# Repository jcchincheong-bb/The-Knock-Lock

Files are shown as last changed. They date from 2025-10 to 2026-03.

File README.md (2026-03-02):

# Knock Lock

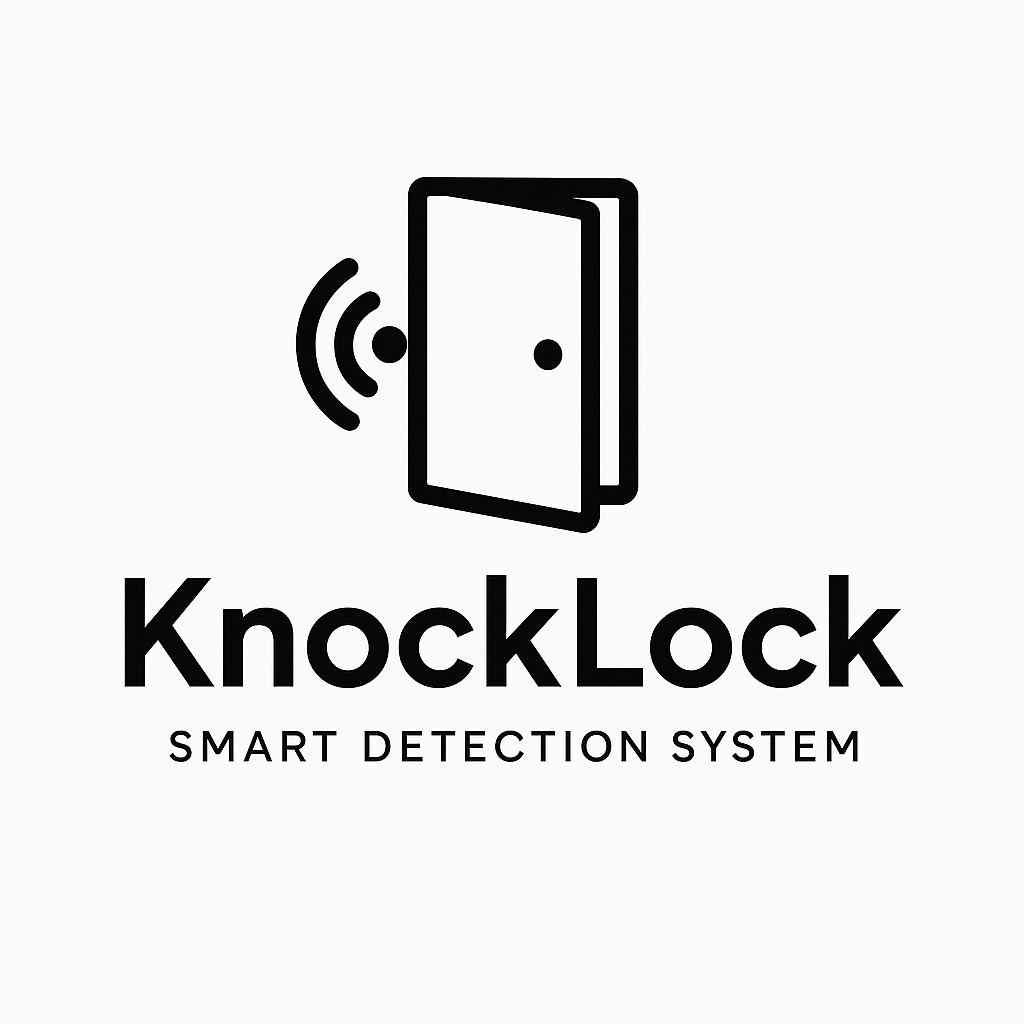
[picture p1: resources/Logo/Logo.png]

<!-- <div id="logo" align="center">
<figure>
  <img src="/resources/Logo/Logo.png" alt="Logo" width="400">
</figure>
</div> -->

As children, many of us might have invented secret knocks that we used to identify ourselves to our friends or siblings. But, what if those special codes could actually unlock the door itself? As adults, how many times have you forgotten your keys and wished you could just knock in a certain way and the door would unlock for you? As such, the aim of The Knock Lock project is to design and assemble a system that unlocks a door by recognising a specific knocking pattern. As a proof of concept, the system will be designed as a small lock box with the hope of extending the idea to work on a full door in the future.

This project was done as part of the course 2314 Practical Electronics at HSRW. The full project report can be found [here](https://github.com/AbhinavK02/Knock-Lock/blob/main/ProjectReport.md).

Knock Lock Product Showcase (https://www.youtube.com/watch?v=qGrgIr3oHPE)

<div align="center">
  <table border="0" style="width: 100%; border: none;">
    <tr>
      <td align="left" style="vertical-align: middle; width: auto; padding: 10px 0;">
        by: <a href="https://abhinavk02.github.io/">Abhinav Kothari</a> and <a href="https://jcchincheong-bb.github.io/">Justin Chin Cheong</a>
      </td>
      <td align="right" style="vertical-align: middle; width: 1%; white-space: nowrap; padding-left: 20px;">
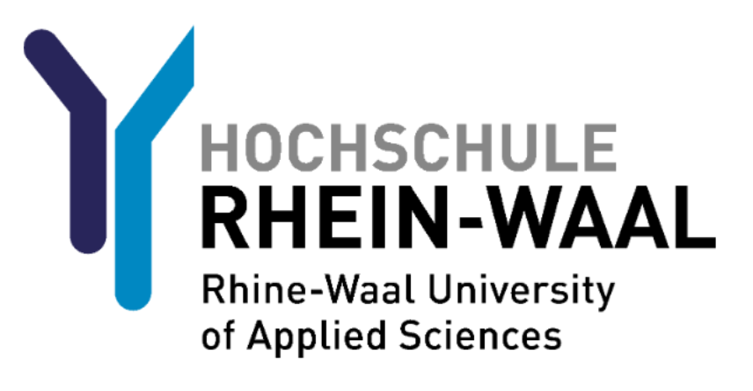
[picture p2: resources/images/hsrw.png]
HSRW Logo
        
      </td>
    </tr>
  </table>
  </figure>

</div>

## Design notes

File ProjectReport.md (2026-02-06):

<!----------------------------------------------------------------
<div id="logo" align="center">
<figure>
  <img src="/resources/images/Logo.png" alt="Logo" width="400">
  <figcaption align="center"><b>Figure 1:</b> Knock Lock Logo</figcaption>
</figure>
</div>

<div id="pcb-blank"  align="center">
  <figure>
  <table border="0">
    <tr>
      <td><figure>
        <img src="/resources/images/Unsoldered PCB.jpeg" height="200">
        <figcaption align="center"><b>(a):</b> Front </figcaption>
      </figure></td>
      <td><figure>
        <img src="/resources/images/Unsoldered PCB 2.jpeg" height="200">
        <figcaption align="center"><b>(b):</b> Back </figcaption>
      </figure></td>
    </tr>
  </table>
  <figcaption align="center"><b>Figure 5.8:</b> Final PCB without Components</figcaption>
  </figure>
</div>
----------------------------------------------------->
<!--
STOP CHANGING THE STRUCTURE! IT'S GOOD NOW!!!
-->
# Knock Lock

<div id="logo" align="center">
<figure>
  
</figure>
</div>

<div align="center">
  <table border="0" style="width: 100%; border: none;">
    <tr>
      <td align="left" style="vertical-align: middle; width: auto; padding: 10px 0;">
        by: <a href="https://www.linkedin.com/in/abhinav-kothari-2ak/">Abhinav Kothari</a> (33349) and <a href="https://jcchincheong-bb.github.io/">Justin Chin Cheong</a> (34140)
        <br><br>
        <strong>Faculty of Technology and Bionics</strong>
        <br><br>
        <em><strong>Rhine-Waal University of Applied Sciences</strong></em>
        <br><br>
        Date: 18 January 2026
      </td>
      <td align="right" style="vertical-align: middle; width: 1%; white-space: nowrap; padding-left: 20px;">
        HSRW Logo
      </td>
    </tr>
  </table>
  </figure>
</div>

<!-- by: [Abhinav Kothari](https://www.linkedin.com/in/abhinav-kothari-2ak/) (33349) and [Justin Chin Cheong](https://jcchincheong-bb.github.io/) (34140) -->

<!-- **Faculty of Technology and Bionics** -->

<!-- ***Rhine-Waal University of Applied Sciences*** -->

<!-- Date: 18 January 2022  -->

----

## Abstract

The Knock Lock project presents the design, implementation, and evaluation of a novel access control system that unlocks a small lock box through the recognition a user-defined knocking pattern. Motivated by the limitations of conventional key-based and electronic locking mechanisms, the system aims to provide a fun and intuitive alternative that does not rely on physical tokens or wireless credentials. Unlike most existing knock-based systems that use piezoelectric sensors, this project explores the use of a MEMS accelerometer for knock detection, enabling improved reliability, flexibility and multi-axis measurement.

Following a V-model design methodology, the system was developed from defined requirements through hardware, software, and housing design, to full system integration and testing. The final prototype consists of an ESP32-based controller, an accelerometer sensor, a servo-driven locking mechanism, a custom PCB, a user interface employing LEDs and a buzzer and a custom 3D printed housing. Verification and validation tests demonstrate reliable knock pattern recognition, successful locking and unlocking behaviour, effective power management with sleep modes, and positive user acceptance.

The results confirm the feasibility of accelerometer-based knock recognition for access control applications and highlight the potential for further development toward full-scale door locking systems and enhanced security features.

## Table of Contents

[[_TOC_]]
<!--------------------------------------------------------------------------------------------------------------------->
<!--------------------------------------------------------------------------------------------------------------------->
## 1 Introduction 
### 1.1 Rationale
As children, many of us might have invented secret knocks that we used to identify ourselves to our friends or siblings. But, what if those special codes could actually unlock the door itself? As adults, how many times have we forgotten your keys and wished you could just knock in a certain way to unlock the door? 

There are many different types of security systems on the market that use systems ranging from combinations to NFC, but there are no commercial products of this kind that unlock by recognising a specific knocking pattern. As such, the aim of The Knock Lock project is to design and assemble a system that unlocks a door by recognising a specific knocking pattern. As a proof of concept, the system is designed as a small lock box as shown in [Figure 1.1](#preliminary-sketch) with the hope of extending the idea to work on a full door in the future.

<div id="preliminary-sketch" align="center">
<figure>
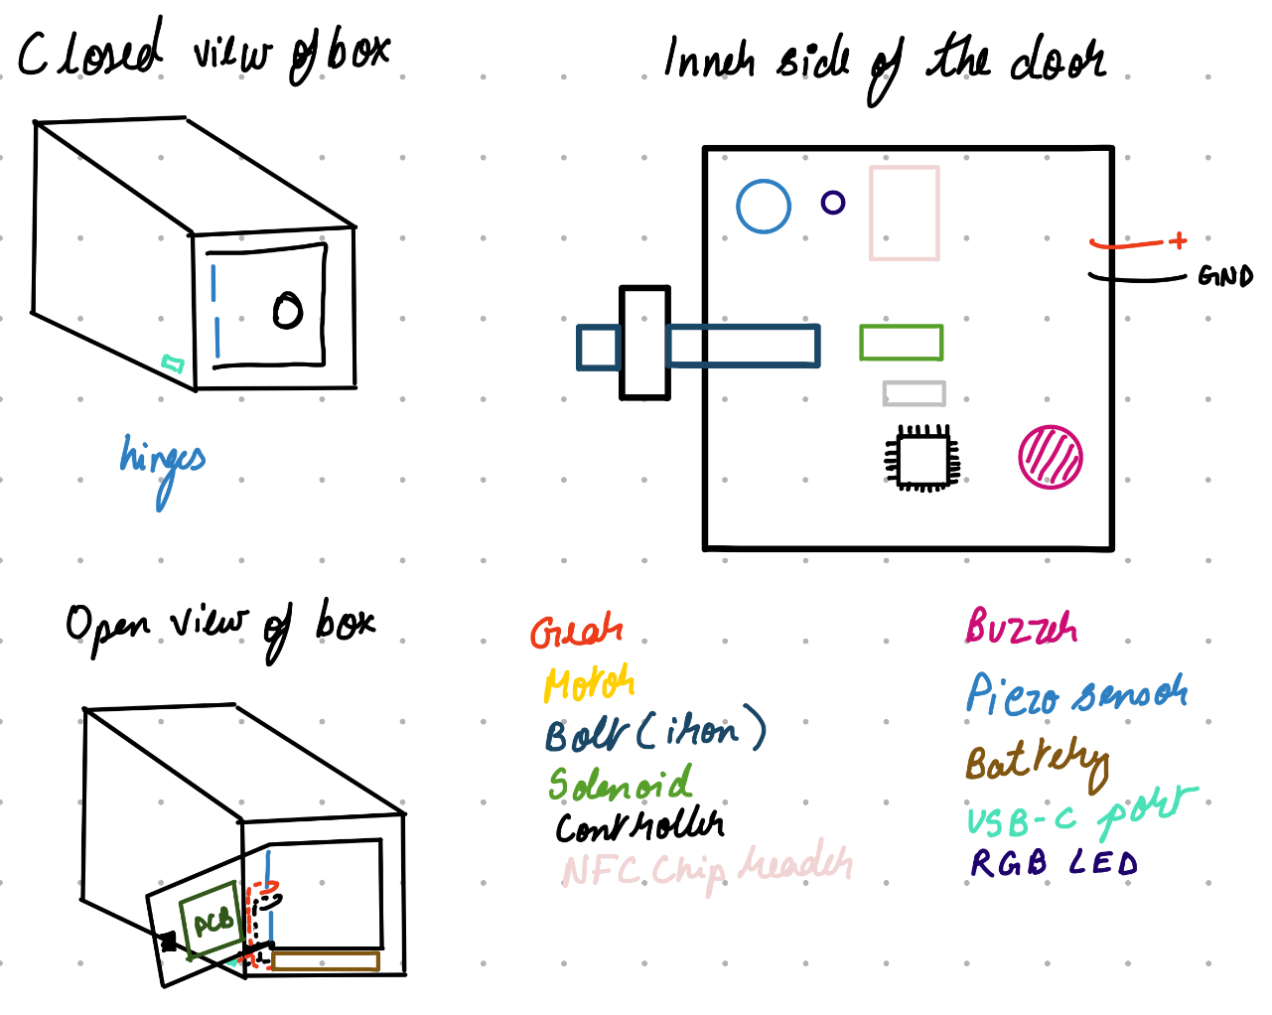
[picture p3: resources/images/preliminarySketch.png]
preliminary-sketch
  
  <figcaption align="center"><b>Figure 1.1:</b> Preliminary Sketch of the Knock Lock</figcaption>
</figure>
</div>

### 1.2	Outline
This report documents the complete development and verification process of the Knock Lock project from conception to assembly to testing. 

[Chapter 1](#1-introduction) introduces the problem with current security systems which the Knock Lock project is trying to solve as well as the project team and their contributions to the project's development. However, before the actual development can be explained, a review of any existing solutions must be done to understand how others approached the problem as discussed in [Chapter 2](#2literature-review). Further, a number of key concepts such as accelerometers and servo motors are discussed in [Chapter 3](#3theory) to establish a theoretical foundation for the project's design. 

In [Chapter 4](#4methodology-and-design), the presentation of the actual development process begins with the definition of the V-model design flow ([4.1](#41-design-approach)) and system requirements ([4.2](#42-system-requirements)). The system is then designed at the highest level with the system architecture ([4.3](#43-system-architecture)) before going into the details of the intended hardware ([4.4](#44hardware-design)), software ([4.5](#45-software-design)) and housing design ([4.6](#46-housing-design)). In keeping with the V-model, verification methods are defined for both before ([4.7](#47-pre-implementation-verification-methods)) and after ([4.8](#48-post-implementation-verification-methods)) implementation. Validation ([4.9](#49-validation-methods)) of the system is also discussed and how the system could be tested against the needs of the user.

After defining the intended design and test specifications, the actual implementation, results and issues are explained in [Chapter 5](#5results). Here the results of prototyping ([5.1](#51-pre-implementation-verification-results)) are treated and their impact on the components used ([5.2](#52-component-selection)) and PCB design ([5.3](#53-pcb-design)) are explored. The process of actually assembling the PCB ([5.4](#54-pcb-assembly)) and developing the software ([5.5](#55-software-implementation)) is described as well as the issues encountered. The construction of the housing ([5.6](#56-housing-prototype)) and the complete list of materials ([5.7](#57-bill-of-materials)) used is also illustrated. Finally, the system's verification ([5.8](#58-post-implementation-verification-results)) and validation ([5.9](#59-validation-results)) results are presented.

Finally, [Chapter 6](#6discussion) discusses how the results of the Knock Lock compares to other projects ([6.1](#61-product-evaluation)) and expounds upon the limitations([6.2](#62-product-limitations)) and significance ([6.3](#63-product-significance)) of the product's performance. [Chapter 7](#7conclusion) concludes the report with a summary of the development journey and outlines some potential future work ([7.1](#71-future-improvements)) for the project.

### 1.3 Project Team
The project team consists of two Mechatronics Engineering Students whose responsibilities in the project were divided
as follows:
- Abhinav Kothari (33349):
  - Design of power regulation, sensor system and human machine interface circuits
  - Development of complete program software
  - Design of preliminary PCB layout
  - Design and refinement of final prototype housing
- Justin Julius Chin Cheong (34140): 
  - Component selection
  - Design of power protection, programming interface and lock actuator circuits
  - Design and refinement of final PCB layout
  - Design of preliminary prototype housing
- Both: 
  - Soldering and assembly
  - Verification of components and system integration
  - Validation of functionality and user acceptance

With regard to writing of this report, the following illustrates the contributions of each team member:
- Abhinav Kothari (33349): 
  - Chapter 2
  - Chapter 4: 4.2, 4.5, 4.6
  - Chapter 5: 5.4, 5.5, 5.6, 5.9
  - Chapter 6
  - Chapter 7
- Justin Julius Chin Cheong (34140): 
  - Chapter 1
  - Chapter 3
  - Chapter 4: 4.1, 4.2, 4.3, 4.4, 4.7, 4.8, 4.9
  - Chapter 5: 5.1, 5.2, 5.3, 5.7, 5.8
<!--------------------------------------------------------------------------------------------------------------------->
<!--------------------------------------------------------------------------------------------------------------------->
## 2	Literature review
In pursuit of unique and easy methods for users to unlock systems, many developments have been made. These methods for unlocking vary from NFCs to Biometric. Knock detection is also a method used in some small scale (non-commercial) projects, which allows for unlocking even without carrying tangible assets (For example a card for NFC unlocking). This section covers the existing projects implementing knock detection, and compares them to a new possible approach which has not been so commonly used in these systems.

### 2.1 Related Work
Reviewing hobbyist and academic projects, gives us an overview of the common techniques used to accomplish this task. Notable implementations [[1,2,3](#9references)] show reliable interpretation of knocks using a piezoelectric elements. However all had some limitations shown from the demonstration. The knock detection was only on a surface parallel to the piezo element. They all had also relatively hard knocks for detection. Some projects pointed out that increasing precision also increases the number of false positives. Even after more research, no projects using accelerometers were found. From reviewing the projects further, it can also been seen that none of the systems implemented a sleep mode for a more power efficient approach.

For processing most the projects implemented and Arduino Deumilanove or an Arduino Nano, and used gear reduction motors, solenoids or servo for locking/unlocking mechanism. Other than the controller used, it is essential to choose the right sensor for knock detection.

### 2.2 Technical Comparison of Sensors
As noted from the previous section, no accelerometers were used in the project, which particularly interesting considering, they are commonly used in high-end consumer electronics such as smartphones for detecting back taps, which work reliably. Hence this section compares the three sensor technologies (Piezoelectric, capacitive accelerometers, vibration sensor) to better understand the situation.

While piezoelectric transducers offer a good signal to noise ratio, they also act as high pass filters. This property provides them with a higher sensitivity for higher frequency vibrations, but hence not the ideal solution for lower frequency vibrations, which is more similar to human knocks [[4](#9references)]. While this blog [[4](#9references)], compares accelerometers with professional piezoelectric sensors, which are much more sensitive than the piezoelectric transducers used in other projects, the same fundamental limitation applies to them as well. Especially considering, vibrations when traveling through various materials may lose high frequency energy relatively quickly, depending on the material property and thickness, which may make it even harder to detect. On the other hand accelerometers allow sensing of flat responses (0Hz) and hence have good sensitivity for even lower frequencies [[4](#9references)]. Vibration sensors allow for detecting only above a specified frequency, depending on its calibration. Moreover, piezoelectric transducers are analog passive devices, hence have quite less power consumption, however also implies they must be always awake to read. 

Vibration sensor have limited customisability due to their digital nature. They can either detect a knock or not, which can potentially cause problems differentiating general environmental vibrations from intentional knocks.

Accelerometers generally have chips to process and amplify signal which can communicate the information using I2C or SPI communication instead of piezoelectric transducers, which as stated earlier are analog or vibration sensor which are digital. This implies, theoretically, an accelerometer should allow for much more customisability via software, as the chips also have many in-built interrupts, which can help make the system more efficient. Moreover, the chips are able to process readings quite well to reduce noise. An accelerometer, being 3-axis, may also allow detection direction of knock which could be helpful in certain scenarios.

A summary of all the differences between piezos, MEMS accelerometers and vibration sensor is shown in [Table 2.1](#PiezoVsAccelVsVibration)

*Table 2.1: Comparison of Piezo, Vibration Sensors and MEMS Accelerometer*

| Feature | Piezoelectric Buzzer | Digital Vibration Sensor | MEMS Accelerometer (Capacitive) |
| :--- | :--- | :--- | :--- |
| **Sensing Principle** | Piezoelectric (Acoustic/Resonant) | Spring-and-Ball (Mechanical Switch) | **Capacitive (Proof-Mass Displacement)**  |
| **Output Type** | Raw Analog Voltage (Uncalibrated) | Digital Binary (HIGH/LOW) | **Digital Data (I2C/SPI)** |
| **Detection Axis** | Single Axis (Directional) | Omni-directional (Uncalibrated) | **3-Axis (X, Y, Z) Sensing** |
| **Customizability** | **Low:** Fixed by hardware/surface| **None:** On/Off trigger only | **High:** Software-defined thresholds |
| **Power Management** | Requires constant CPU sampling | Interrupt-capable | **Integrated Interrupts (Deep Sleep)** |
| **Primary Limitation** | High-frequency bias (Acoustic) | Lack of pattern sensitivity | Higher initial code complexity |
| **Cost** | Extremely Low | Low | Moderate |

These sensors are then compared in [Section 4.4.2](#442-sensor-sub-system) and results can be found in [Section 5.1.1](#511-concept-feasibility)

<!--------------------------------------------------------------------------------------------------------------------->
<!--------------------------------------------------------------------------------------------------------------------->

## 3	Theory
Building upon the sensor characteristics identified in [Section 2](#2-literature-review), this sections outlines the fundamental theoretical concepts required to implement the system effectively. These concepts relate to the different aspects of the system's circuit design and are required for fully understanding the design created. 

### 3.1 Accelerometers
Capacitive accelerometers are sensors used to measure acceleration forces by detecting changes in capacitance. They typically consist of a small movable mass suspended between fixed electrodes as seen in [Figure 3.1](#imu)[[6](#9references)]. When acceleration is applied, the mass shifts, altering the distance between the electrodes and therefore changing the capacitance. This change is proportional to the applied acceleration and is converted into an electrical signal.

<div id="imu" align="center">
<figure>
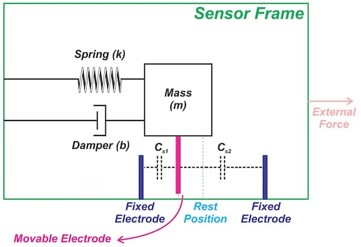
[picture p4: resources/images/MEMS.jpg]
  
  <figcaption align="center"><b>Figure 3.1:</b> Diagram of Capacitive Accelerometer Working Principle</figcaption>
</figure>
</div>

The Knock Lock project uses an accelerometer as the main sensor for knock detection. Initial testing revealed that these accelerometers are very well suited for detecting knocks (See [Section 5.1.1](#511-concept-feasibility)) compared to piezoelectric devices, which use the piezoelectric effect to convert mechanical vibrations into voltage to be detected. The sensor's role in the design is discussed in [Section 4.4.2](#442-sensor-sub-system).

Most modern capacitive accelerometers are sold as integrated circuits (ICs) with three accelerometers (one for each axis) as well as signal conditioning electronics and an I2C interface [[7](#9references)].

### 3.2 I2C
Since most accelerometers use I2C to communicate, it is necessary to include I2C interface and connections in the circuit design as discussed in [Section 4.4.4](#444-controller-sub-system).

I2C is a synchronous, serial communication protocol commonly used for short-distance communication between integrated circuits [[7](#9references)]. It uses two shared lines: a serial data line (SDA) and a serial clock line (SCL). Devices on the bus are identified by unique addresses and operate in a master–slave configuration. I2C allows multiple devices to communicate using the same bus, reducing wiring complexity. [Figure 3.2](#i2c) taken from [[7](#9references)] shows how a typical I2C device connects with a microcontroller.

<div id="i2c" align="center">
<figure>
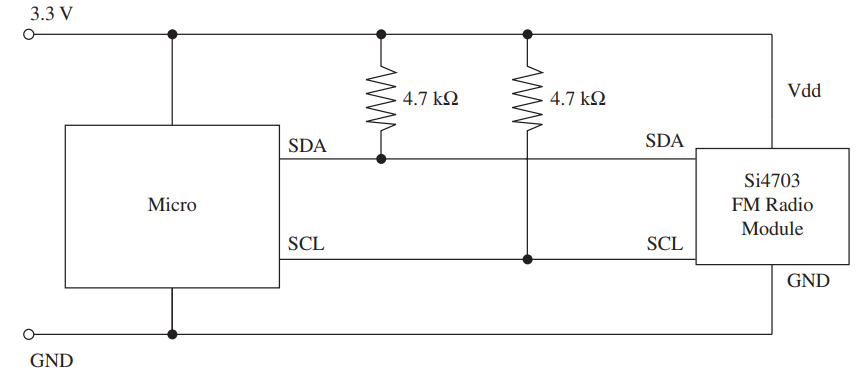
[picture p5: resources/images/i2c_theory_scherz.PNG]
  
  <figcaption align="center"><b>Figure 3.2:</b> Diagram of I2C Connection</figcaption>
</figure>
</div>

### 3.3 High-Side Driver
To perform the actual locking and unlocking after the system recognises knocks with the [accelerometer](#31-accelerometers), the system needs a lock actuator. To interface this actuator, a high side driver is used as described in [Section 4.4.3](#443-lock-actuator-sub-system). It is essentially used to cut power to the actuator in sleep mode to reduce power consumption.

High-side drivers are electronic circuits used to control a load by switching the high voltage side of the load. They are typically implemented using transistors or integrated driver ICs and allow a microcontroller to safely control high-voltage or high-current loads such as motors, relays, or solenoids [[8](#9references)]. [Figure 3.3](#highDriver) taken from [[8](#9references)] shows how a typical high side driver configuration for use with a microcontroller. The microcontroller controls the base of the transistor. When it is set to low, the transistor does not conduct and the gate of the MOSFET is pulled up. This means the gate-source voltage of the MOSFET is 0V and thus, it does not conduct and the motor is cut off from power. When the base of the transistor is set high, the opposite occurs and the gate of the MOSFET is pulled down to ground causing the MOSFET to trigger and connect the motor to power.

<div id="highDriver" align="center">
<figure>
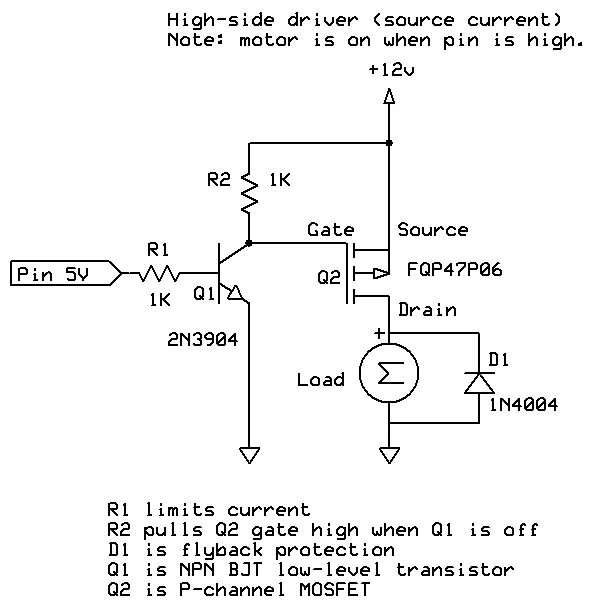
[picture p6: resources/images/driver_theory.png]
  
  <figcaption align="center"><b>Figure 3.3:</b> Diagram of High Side Driver Circuit</figcaption>
</figure>
</div>

### 3.4 Servo Motor
With the high side driver as the interface, the actual lock actuator is a servo motor as described in [Section 4.4.3](#443-lock-actuator-sub-system).

Servo motors are electromechanical devices used for precise control of angular position, speed, and torque. A typical servo motor consists of a DC motor, a gearbox, a position sensor (usually a potentiometer), and a control circuit. The motor position is controlled using a pulse-width modulation (PWM) signal, where the pulse width determines the desired angle as shown in [Figure 3.4](#servo)[[7](#9references)]. 

<div id="servo" align="center">
<figure>
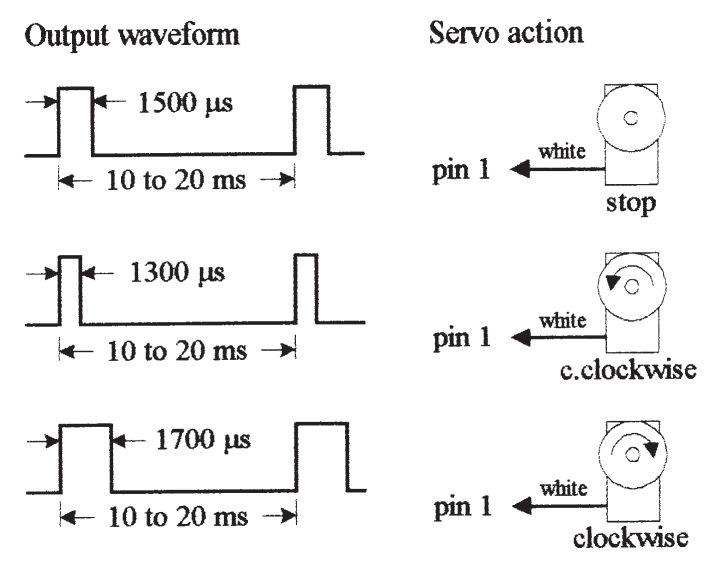
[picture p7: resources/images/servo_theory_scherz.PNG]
  
  <figcaption align="center"><b>Figure 3.4:</b> Diagram of Servo Motor Working Principle</figcaption>
</figure>
</div>
<!--------------------------------------------------------------------------------------------------------------------->
<!--------------------------------------------------------------------------------------------------------------------->

## 4	Methodology and Design
With the theoretical foundation established, the actual development process can be outlined, beginning with the [design approach](#41-design-approach).

### 4.1 Design Approach <!-- V-model-->
Due to the high complexity of the project, the project team decided to use the V-model design flow. With this approach of continuous verification, the project team aimed to reduce risk by finding issues and their solutions early.

### 4.2 System Requirements <!-- Requirements, not specs -->
To fully implement the system, a number of requirements related to function, technology and project management have been outlined. 

#### 4.2.1 Functional Requirements

For Knock Knock Lock Box to be a satisfiable product, the following functional requirements must be implemented:

- It unlocks within 1-2 seconds when a specific knocking pattern is used on the surface of the box
- It indicates turns a green LED on and simultaneously plays a simple beep to indicate that the box has been unlocked
- It rejects pattern if incorrect within 1-2 seconds after knocking has ended
- It turns a red LED on and simultaneously plays a simple alarm to indicate that the knocking pattern was false or unrecognised
- It alerts when the battery level drops below a certain level by flashing a red LED, even in power saving mode
- It only powers on after some initial knock to wake up the system, on wake it shows an yellow LED
- If no knocks detected for 60 seconds, it goes back to power saving mode
- It has provision to use a additional port as an alternative power source in case battery dies out, with no prospect to upload firmware through it
- It uses some actuator for unlocking and locking 
- It has a programming mode where the user sets the knock for the system to recognise, mode can only be entered when the box is unlocked 

#### 4.2.2 Technical Requirements

For the Knock Knock Lock Box to operate and perform its functions, the following technical requirements must be implemented:

- The sensor system can detect knock amplitudes and output a measurable reading to the microcontroller
- There are provisions to protect the sensor and microcontroller from voltage spikes that might occur from the power supply
- The microcontroller software can detect up to 30 knocks with consecutive knocks being less than 2s apart and match the timings to the predefined knock pattern with a set tolerance of acceptance
- The power supply is a battery with a working voltage of 3.2V to 6.5V
- The enclosure can protect the system within a typical indoor environment (IP 31)
- The provision to set microcontroller to low power mode and wake it back up
- Should function at temperatures ranging 0-40°C and humidity 10-90%

#### 4.2.3 Project Requirements

For the Knock Knock Lock Box project to produce a functional product upon close out, the following project requirements must be met:

- the budget is 25€ not including the PCB or mechanical components
- the project workload is estimated at 240h
- all components used for the project must be ordered from mouser.de or taken from the in-house supply  at HSRW
- the project schedule adheres to the following deadlines
    - Schematic Design: 2025-10-26
    - PCB Design Draft: 2025-11-09
    - PCB Design and Partslist: 2025-11-23
    - PCB Assembly: 2025-12-20
    - Project Report: 2026-01-18
    - Project Presentation and Demo: 2026-01-21

### 4.3 System Architecture <!-- FSD and maybe specs -->
From the requirements outlined in [Section 4.2](#42-system-requirements), a system architecture was designed as shown in [Figure 4.1](#fsd). 

<div id="fsd" align="center">
<figure>
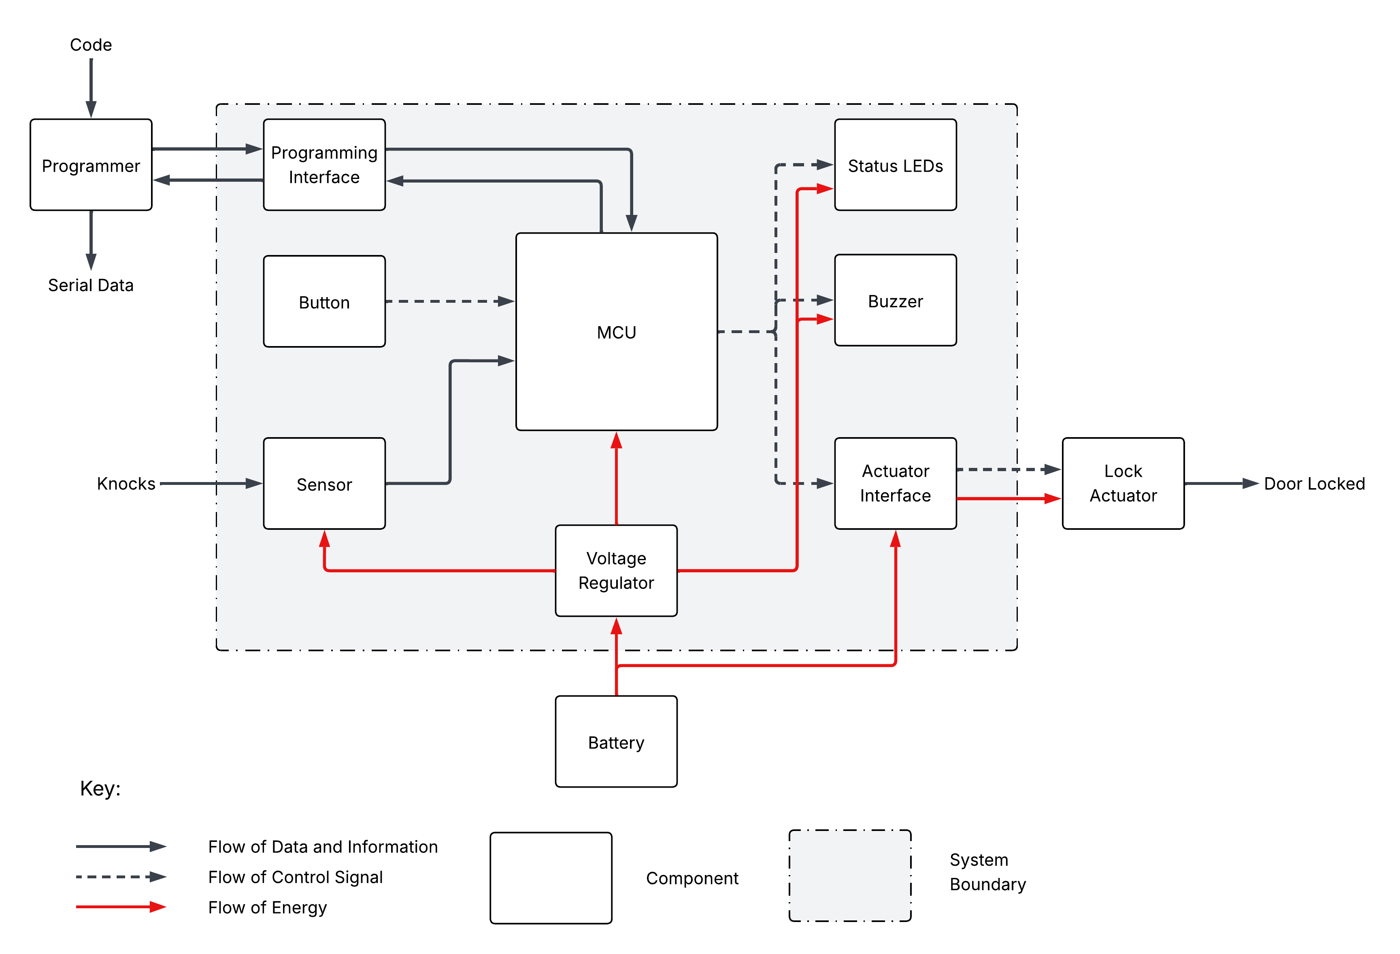
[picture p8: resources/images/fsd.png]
fsd
  
  <figcaption align="center"><b>Figure 4.1:</b> Functional Structure Diagram of Entire System</figcaption>
</figure>
</div>

### 4.4	Hardware Design <!-- Schematics, explanations and component specifications -->
#### 4.4.1 Full Schematic Design
The next layer after the [system architecture](#43-system-architecture) was defined as the schematic of the system as shown in [Figure 4.2](#schematic). In designing the schematic, each of the sub-systems defined in [Figure 4.1](#fsd) were treated separately before integrating together.

<div id="schematic" align="center">
<figure>
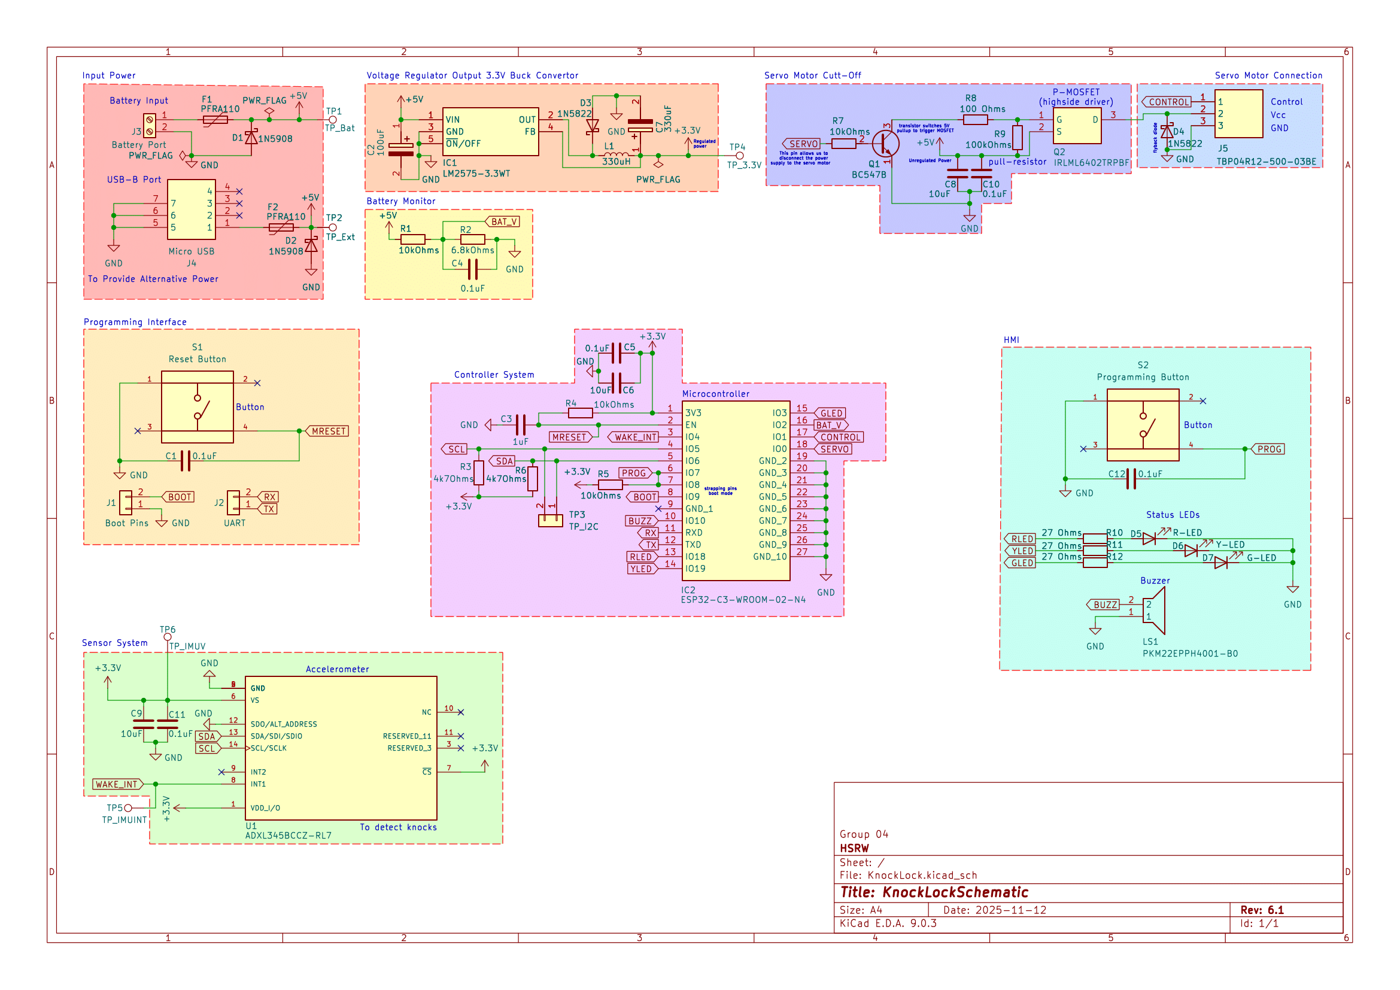
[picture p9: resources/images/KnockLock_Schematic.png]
schematic
  
  <figcaption align="center"><b>Figure 4.2:</b> Full Schematic of the System</figcaption>
</figure>
</div>

The following sections discuss the design of the schematic as well as the specifications of the most important components for each sub-system. 

#### 4.4.2 Sensor Sub-System
The first of the sub-systems is the sensor sub-system as shown in [Figure 4.3](#sensor-sch). 

<div id="sensor-sch" align="center">
<figure>
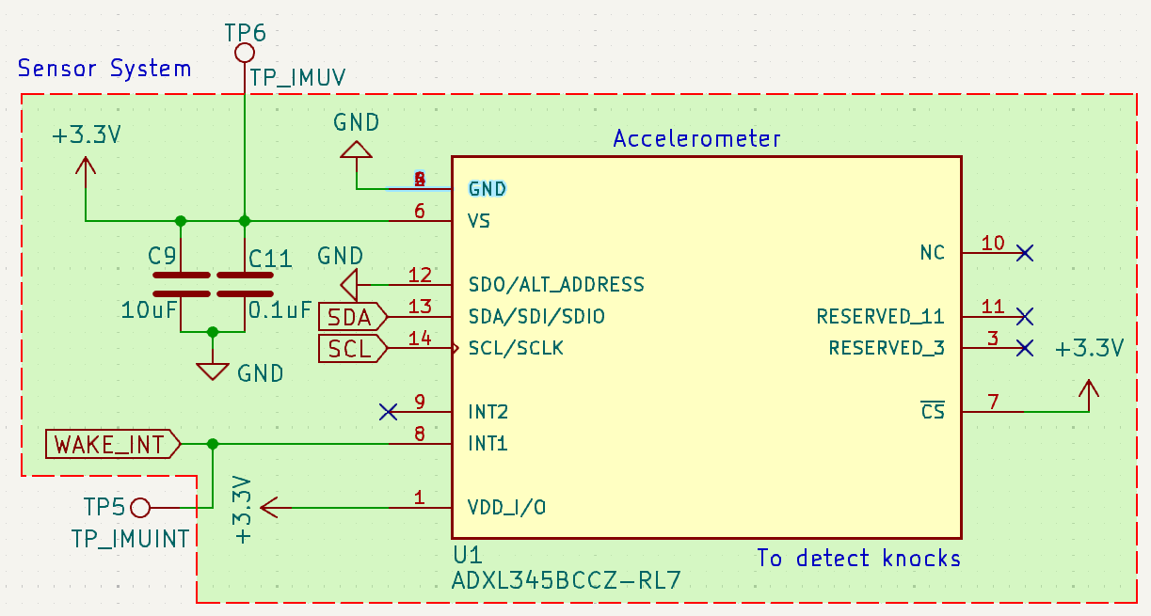
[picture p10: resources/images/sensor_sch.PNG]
sensor-sch
  
  <figcaption align="center"><b>Figure 4.3:</b> Schematic of the Sensor Sub-System</figcaption>
</figure>
</div>

As mentioned in the [Section 2 Literature Review](#2literature-review), most existing projects implemented a piezo element over an accelerometer or a vibration sensor to detect knocks. However, [Table 2.1](#PiezoVsAccelVsVibration) also revealed the potential efficacy of using an accelerometer instead of a piezo. Thus, to identify an appropriate sensor for the most accurate and reliable knock detection, a simple comparative experiment must be conducted. A piezo disc (DAOKAI JA-DA-036 27mm) wass tested against an accelerometer development module (JOY-IT SEN-MMA8452Q) which was readily available in the lab. Note the vibration sensor is excluded from this comparative testing as with its preliminary testing it was revealed that it has significant reliability issues. The sensor lacked the necessary sensitivity control, often oscillating between over-sensitivity (detecting ghost knocks) and under-sensitivity.

The sensors are tested in two different scenarios: a thin plastic lid and on a wooden chair as seen in Figures [4.4](#sensorTestPlastic) and [4.5](#sensorTestWood) respectively. This allowed for understanding how each sensor performed on materials of very different densities and stiffness's. In each test, the sensors are attached to the surface and connected to an Arduino UNO for processing the output. Knocks are then applied to the opposite side of the material and the readings are recorded and compared.

<div id="sensorTestPlastic" align="center">
<figure>
  Testing setup 1 - Plastic
  <figcaption align="center"><b>Figure 4.4:</b> Testing Setup 1 - Plastic</figcaption>
</figure>
</div>

<div id="sensorTestWood" align="center">
<figure>
  Testing setup 2 - Wood
  <figcaption align="center"><b>Figure 4.5:</b> Testing Setup 2 - Wood</figcaption>
</figure>
</div>

The sensors are compared based on two criteria. 
1. Reliability of detecting knocks of different strengths in each setup
2. Reliability of detecting knocks of different speeds in each setup

The results of this comparative test and the final sensor decision are presented in [Section 5.2.1](#521-sensor-selection). 

The general expectation was that both sensors would exhibit similar accuracies, with accelerometer being only slightly better when it came to detection through a thicker surface, and since the piezo is significantly cheaper and consumes less current, the piezo would be the ideal sensor.

#### 4.4.3 Lock Actuator Sub-System
On the other end of the system is the locking mechanism which is accomplished through a lock actuator. The circuit to interface this actuator is shown in [Figure 4.6](#lock-actuator-sch). 

<div id="lock-actuator-sch" align="center">
<figure>
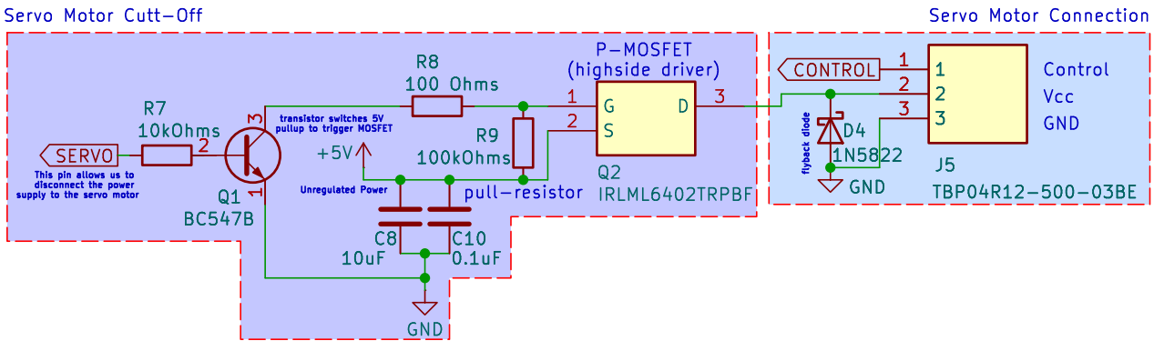
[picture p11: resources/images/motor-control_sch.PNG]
lock-actuator-sch
  
  <figcaption align="center"><b>Figure 4.6:</b> Schematic of the Lock Actuator Sub-System</figcaption>
</figure>
</div>

The initial concept of the product as shown in [Figure 1.1](#preliminary-sketch) envisioned the use of a solenoid actuator to work similarly to the bolt in a door. However, another component which could accomplish the locking while also being cheaper and using less power is a simple servo motor. As such, a number of options for both were found on Mouser for consideration and compared in [Table 4.1](#tab:servo-comp). Clearly, the power requirement for the solenoid is much higher than the that of the servo. This would mean either a boost converter or some other additional voltage regulation would be needed to power the solenoid. On top of that, the solenoids are more expensive per unit. As such, the project team opted to use a servo motor and chose the SER0050 since it is a higher torque than the SER0049. 

<div id="tab:servo-comp">

*Table 4.1: Comparison of Solenoids and Servos Available on Mouser*
| Type | Model Number | Price [€] | Voltage [V] | Load Current [mA] | Lock Length [mm] |
| --- | --- | --- | --- | --- | --- |
| Solenoid | 3992 | 6.45 | 5–6 | 800-1000 | 10 |
| Solenoid | 412 | 6.45 | 12 | 300 | 15 |
| Solenoid | 2776 | 4.43 | 5 | 1100 | 3 |
| Servo | SER0050 | 5.16 | 4.8–6 | 110-120 | 15 |
| Servo | SER0049 | 4.30 | 4.8–6 | 110-120 | 15 |
<div>

Another important aspect of the lock actuator interface is the power cut-off system. This is accomplished using a high side driver as described in [Section 3.3](#33-high-side-driver). Essentially, the P-MOSFET (Q2) cuts the actuator's power supply line off when triggered. It is driven by an NPN transistor (Q1) which is driven by the microcontroller. 

#### 4.4.4 Controller Sub-System
Potentially the most important of the sub-systems is the controller sub-system shown in [Figure 4.7](#controller-sch).
<div id="controller-sch" align="center">
<figure>
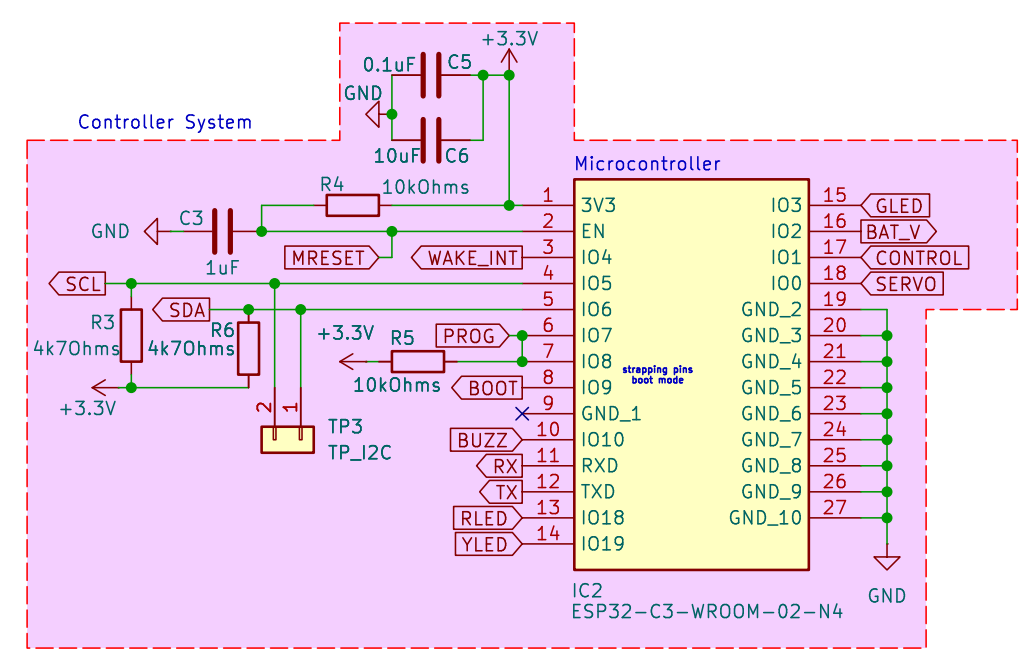
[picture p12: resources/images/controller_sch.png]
controller-sch
  
  <figcaption align="center"><b>Figure 4.7:</b> Schematic of the Controller Sub-System</figcaption>
</figure>
</div>

The microcontroller (MCU) interfaces the sensor, the lock actuator and the human machine interface (HMI). It handles all the processing and runs the program developed in [Section 5.5](#55-software-implementation). The complete pin mapping of the MCU is shown in [Table 4.2](#tab:controller-pin-mapping). 

<div id="tab:controller-pin-mapping">

*Table 4.2: Pin Mapping of Microcontroller*
| Pin | Name  | Type / Label | Description / Connection |
|---:|---|---|---|
| 1 | 3V3 | Power | +3.3V Supply from Regulator |
| 2 | EN | Reset | Enable / Reset connecting to Reset Button |
| 3 | IO4 | WAKE_INT | Wake Interrupt for Sensor |
| 4 | IO5 | SCL | SCL (I2C Clock) with 4.7kΩ Pull-up |
| 5 | IO6 | SDA | SDA (I2C Data) with 4.7kΩ Pull-up |
| 6 | IO7 | PROG | Input to trigger programming mode. Pulled up. |
| 7 | IO8 | - | Strapping pin pulled up for easy booting into UART download mode |
| 8 | IO9 | BOOT | Strapping Pin connected to pin header for booting into UART download mode  |
| 9 | GND_1 | Ground | Not Connected |
| 10 | IO10  | BUZZ | Buzzer | 
| 11 | RXD | RX | UART Receive |
| 12 | TXD | TX | UART Transmit |
| 13 | IO18  | RLED | Red LED |
| 14 | IO19  | YLED | Yellow LED | 
| 15 | IO3 | GLED | Green LED |
| 16 | IO2 | BAT_V | Battery Voltage Monitoring |
| 17 | IO1 | CONTROL | Control signal for Lock Actuator |
| 18 | IO0 | SERVO | Signal to cut-power to Lock Actuator |
| 19–27 | GND | Ground | Main System Ground |
</div>

From [Table 4.2](#tab:controller-pin-mapping), it can be seen that the chosen MCU must have:
- at least 11 programmable GPIOs
- I2C communication
- at least 1 ADC GPIO 
- on-board UART interface 
- exposed enable and strapping pins

Additionally, the chosen MCU must large enough to easily solder onto a PCB. 

Given the ease in which it can be programmed via the Arduino IDE and it's high computation speed and robust features, the project team believed an MCU from the ESP32 line would best fit the specifications. On Mouser, a number of options that met the basic specifications were found as shown in [Table 4.3](#tab:esp32-comp). Ultimately, the decision to chose the ESP32-C3-WROOM-02-N4 [[9](#9references)] was because it was large and had pins exposed on the sides for easier assembly (unlike the 356-ESP32C6MINI1H8) and it was cheaper than the H4 while still meeting all the specifications. This chip also has a lower power consumption sleep mode which draws only 5uA, making it incredibly viable for a low power design.
<div id="tab:esp32-comp"> 

*Table 4.3: Comparison of ESP32 Chips Available on Mouser*
| Part Number | Price [€] | Interfaces | GPIO Count | ADC GPIOs | Size [mm] | Package Type |
| --- | --- | --- | --- | --- | --- | --- |
| ESP32-C3-WROOM-02-N4  | 3.12 | I2C, SPI, UART | 15 | 4 | 18 × 25.5 | Castellated module with exposed pins | 
| ESP32-C3-WROOM-02-H4  | 3.36 | I2C, SPI, UART | 22 | 4 | 18 × 25.5 | Castellated module with exposed pins | 
| 356-ESP32C6MINI1H8 | 4.69 | I2C, SPI, UART | 22 | 6 | 13.2 × 16.6 | Castellated mini module with pins underneath |
</div>

#### 4.4.5 Programming Interface Sub-System
In order to program the [controller sub-system](#442-controller-sub-system), a programming interface as shown in [Figure 4.8](#prog-interface-sch) is required. 

<div id="prog-interface-sch" align="center">
<figure>
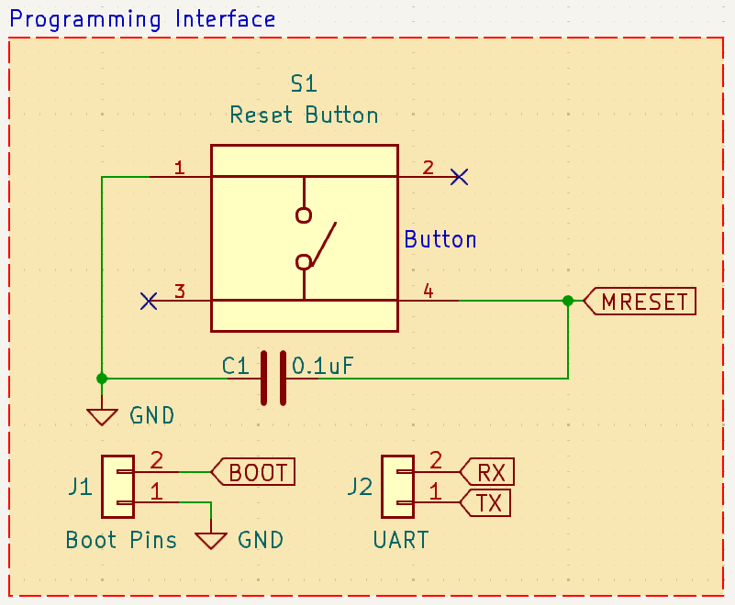
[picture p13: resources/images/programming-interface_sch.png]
prog-interface-sch
  
  <figcaption align="center"><b>Figure 4.8:</b> Schematic of the Programming Interface Sub-System</figcaption>
</figure>
</div>
The design simply uses a pin header which connects to the UART receiver and transmitter pins of the microcontroller so that it can be programmed directly through the on-board UART interface. This is done as opposed to using a USB-to-UART Bridge chip because it requires less components on the PCB and thus lowers costs. The boot pins can be connected with a jumper to pull down the strapping pin and the the button pulls down the enable pin to reset the microcontroller so that it can boot into UART download mode.

#### 4.4.6 Human Machine Interface Sub-System
Since the product has to be used by humans, it requires a human machine interface (HMI) which is illustrated in [Figure 4.9](#hmi-sch). 

<div id="hmi-sch" align="center">
<figure>
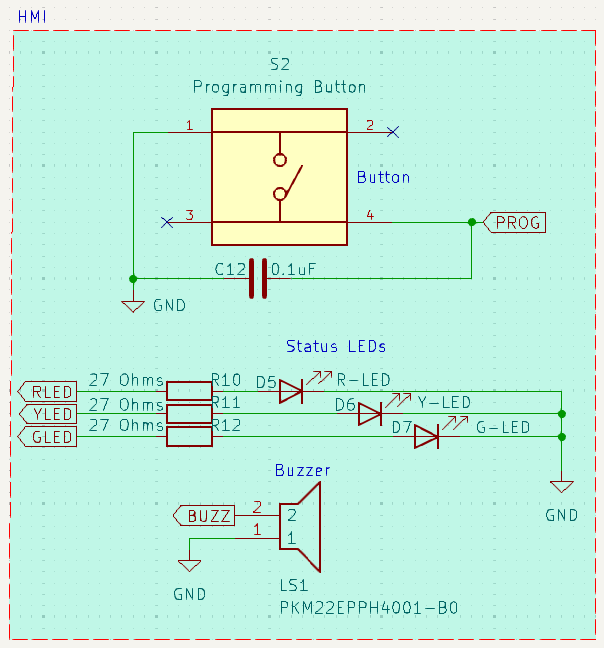
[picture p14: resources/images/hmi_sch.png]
hmi-sch
  
  <figcaption align="center"><b>Figure 4.9:</b> Schematic of the HMI Sub-System</figcaption>
</figure>
</div>

The HMI uses three different LEDs to convey different meanings to the user. The general idea was: 
- the green LED indicates that the box is unlocked
- the yellow LED indicates the box is locked and in stand-by
- the red LED indicates when unlocking attempt was unsuccessful

The buzzer was then intended to create auditory feedback for the same actions as described above. One sound indicates when the box is unlocked successfully. Another for when it is unsuccessful. Here, careful consideration of which frequencies to use on the buzzer must be taken. The loudness of the buzzer should be high enough to be heard through housing, but not so loud as to be uncomfortable for the user. Thus, a sound pressure level of around 80dB is sufficient.

Finally, the HMI includes a simple button which can be used to enter the programming mode of the product. A summary of all the actions the HMI should perform is given in [Table 4.4](#tab:hmi)

<div id="tab:hmi">

*Table 4.4: HMI Actions*
| Mode | User Input | Purpose / Action | System Output |
| --- | --- | --- | --- |
| Locked | Idle | Waiting for input | Yellow LED on |
| Locked | Any knock | Knock registered | Green LED blinks once |
| Locked | Knocking correct pattern | Successfully unlocking | Green LED on, pleasant buzzer sound, actuator unlocks |
| Locked | Knocking incorrect pattern | Unsuccessfully unlocking | Red LED blinks once, unpleasant buzzer sound |
| Locked | Pressing button | Cannot program while locked | Red LED blinks once, unpleasant buzzer sound |
| Locked | Wait 60 s | Go to sleep | All LEDs turn off |
| Unlocked | Idle | Waiting for input | Green LED on |
| Unlocked | Pressing button | Entering programming mode | All LEDs blink once |
| Unlocked | Knocking twice | Re-locking | Yellow LED on, actuator locks |
| Programming | Idle | Waiting for input | Yellow LED on |
| Programming | Any knock | Knock registered | Green LED blinks once |
| Programming | Knock new pattern | Programming new pattern | Buzzer plays back pattern, green LED blinks pattern |
| Programming | Wait 5 s | Programming mode timeout | Red LED blinks once, unpleasant buzzer sound |
| Sleep | Idle | Waiting for input | All LEDs off |
| Sleep | Knock twice | Wake up | Yellow LED on |
</div>

#### 4.4.7 Power Regulation Sub-System
Finally, the system cannot function without reliable power and as such a power regulation system has to be defined as shown in [Figure 4.10](#power-sch). 

<div id="power-sch" align="center">
<figure>
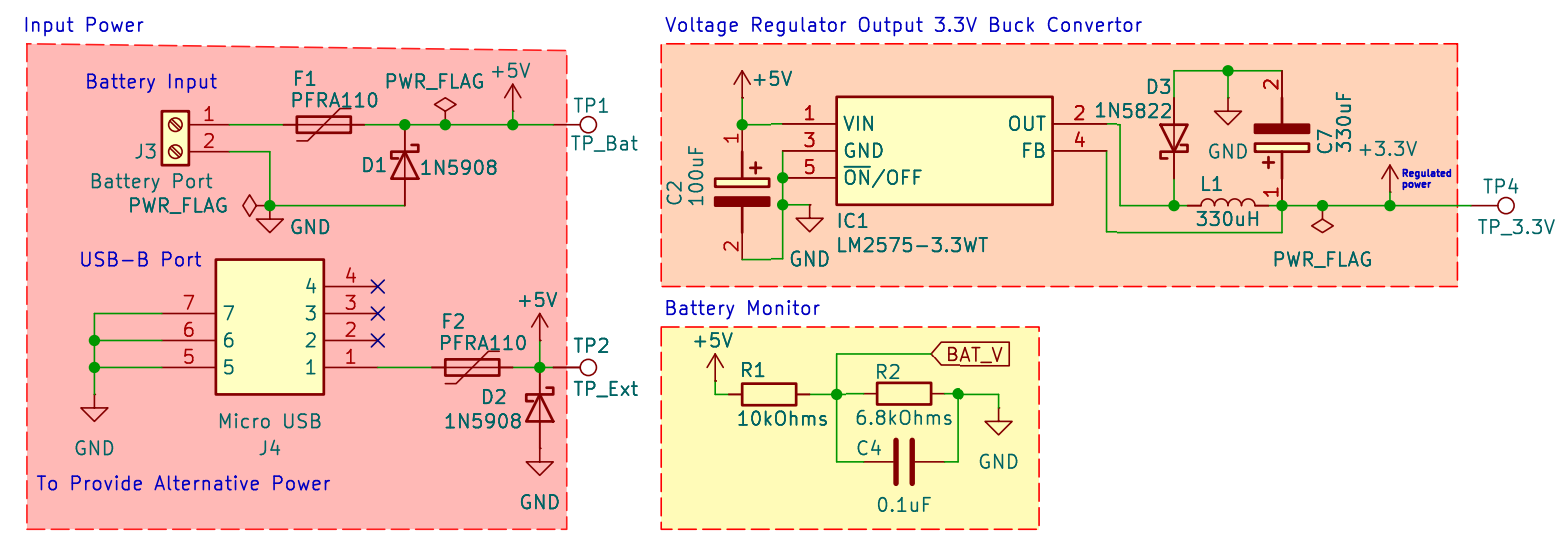
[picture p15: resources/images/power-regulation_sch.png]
power-sch
  
  <figcaption align="center"><b>Figure 4.10:</b> Schematic of the Power Regulation Sub-System</figcaption>
</figure>
</div>

Since the [controller](#444-controller-sub-system) uses an ESP32 which requires 3.3V [[9](#9references)], a voltage regulator that outputs 3.3V is required. The most common and efficient means of accomplishing this is using a higher voltage supply and using regulator to step down the supply. For the purpose of this project, a switching buck converter was chosen instead of using a linear voltage regulator as they are higher efficiency and produce less heat. Mouser has a very large range of switching regulators, many of which meet these minimum specifications. Ultimately, the LM2575-3.3WT was chosen since it was rather cheap, has a maximum input voltage of 40V and typical efficiency of 75%. Additionally, the diode used in the regulation circuit also needs to have low forward voltage drop and low junction capacity so that it provides minimal impede the high-frequency switching.

The voltage regulation must also provide protection in addition to providing the right voltage level. The buck converter itself inherently provides over-voltage protection up to 40V. To implement reverse polarity protection, TVS diodes are used in combination with a fuse. The diode is connected across the junctions such that when a reversed voltage is connected, the diode shorts the external source and not the rest of the circuit. The fuses also provide over-current protection. To dimension the fuse, the specifications of the LM2575-3.3WT were considered. With a maximum output current of 1A, output voltage of 3.3V, efficiency of 75% and input voltage of 6V, the maximum current required by the regulator is around 0.733A. See [Appendix A](#appendix-a-circuit-dimensioning-calculations) for the calculations. Thus, the fuse should safely carry around 1A to account for fluctuations. As such, the PFRA110 was chosen as it has a hold current of 1.1A and a trip current of 2.2A. This fuse is also resettable so after current is cut-off, the fuse can cool down and reset. 

Another interesting aspect of the circuit is the inclusion of an alternative power connection. The battery terminal is meant to be the primary power source via 4S AA batteries and the micro USB port is for emergency powering when the battery dies and the box is locked. It also connects to the voltage regulator and has it's own protection fuse and diode.

Finally, the circuit contains a simple voltage divider that steps down the 5V supply line to less than 3.3V so that it can be read by the ADC on the microcontroller. The voltage at the ADC can then be calculated using a voltage divider ratio. 

#### 4.4.8 Component Specifications  <!-- Table of main components and their most important specs -->
Based on the circuit design and requirements described above, the specifications of the main components of the system are compiled in [Table 4.5](#tabSpecs)

<div id="tabSpecs">

*Table 4.5: List of Component Specifications*
| Component | Main Specifications |
| --- | --- |
| Sensor | Reliably detect knocks of different strengths and at different speeds |
| Lock Actuator | 5 V operation, > 4 mm travel length (suitable for small box) |
| Bipolar NPN Transistor | Maximum collector–emitter voltage > 5 V |
| P-channel MOSFET | Maximum drain–source voltage > 5 V, gate–source threshold voltage < 3.3 V |
| Microcontroller | 11 GPIOs, I2C, 1 ADC GPIO, UART, enable and strapping pins, large package size, exposed pins |
| LEDs | Medium luminous intensity (> 180 mcd) and low power consumption (< 100 mW) |
| Buzzer | Medium sound pressure level (~80 dB) |
| Push Button | Isolating voltage > 5 V |
| 3.3 V Output Voltage Regulator | Input voltage up to 40 V, output voltage 3.3 V |
| TVS Diode | Maximum forward current > 2.5 A, DC blocking voltage > 10 V |
| Schottky Diode | Forward voltage drop < 1 V, low junction capacitance < 1 nF |
| Resettable Fuse | Hold current > 1 A, trip current > 2 A |
| Battery Holder | Holds 4 AA batteries in series |
| AA Battery | 1.5 V |
| Micro USB B | Input voltage > 6 V, durability > 2000 cycles |
</div>

### 4.5 Software Design <!-- Just logic no code yet -->
#### 4.5.1 System Flowchart
<div id="sw-flow" align="center">
<figure>
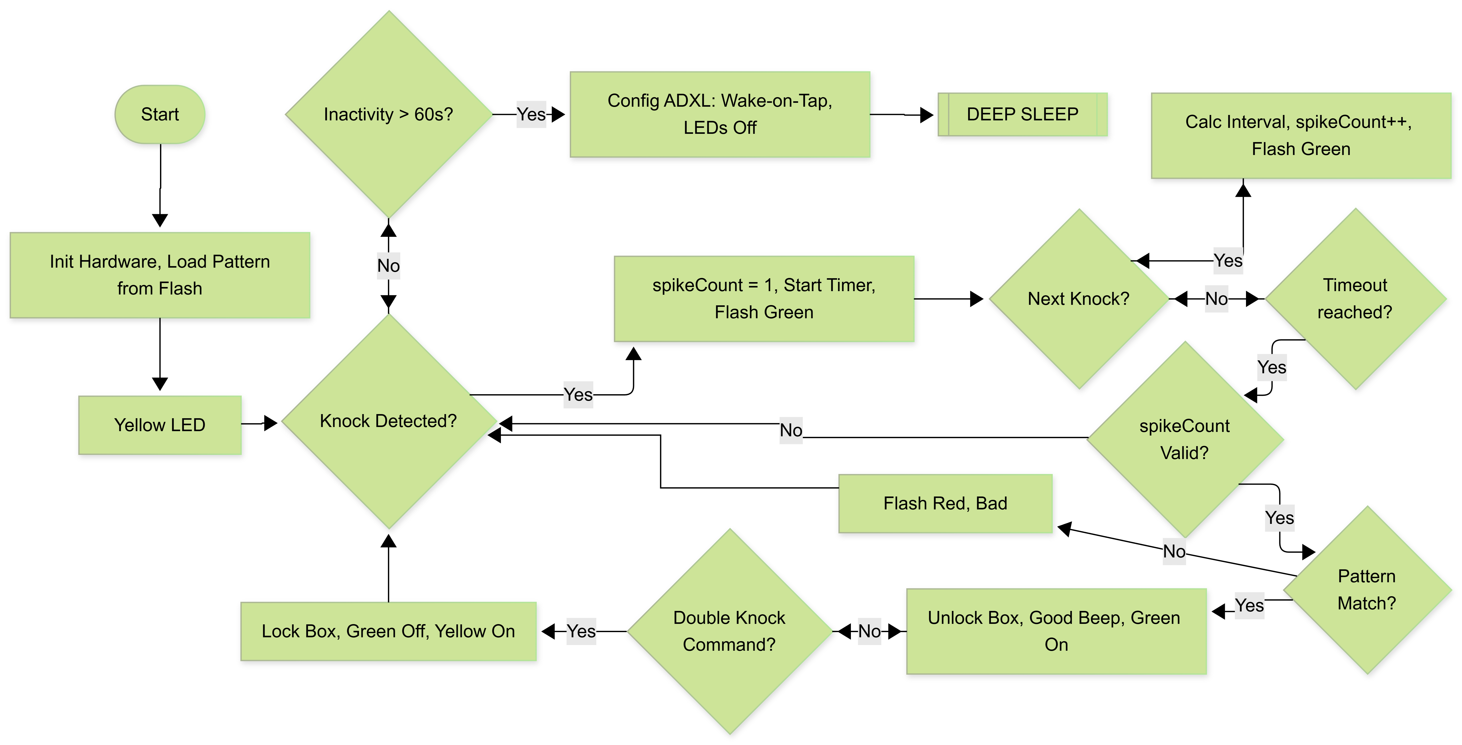
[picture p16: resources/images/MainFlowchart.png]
sw-flow
  
  <figcaption align="center"><b>Figure 4.11:</b> Programming Flowchart of Main System</figcaption>
</figure>
</div>

The flowchart in [Figure 4.11](#sw-flow) shows, how the overall full system must work. The system starts in locked state, where it continuously listens for knocks, unless its asleep, and records them. Once the knocks are recorded, they are checked against the target pattern, if they match, the system unlocks, else it stays locked. Knocking twice locks the box again. LEDs and Buzzer are used to give feedback to the user throughout the system flow.

Interrupts are used to wake the system up from sleep for again starting to read knocks as shown in [Figure 4.12](#sw-flow-isr). If the box is unlocked and the programming button is pressed, the system enters programming mode, where it records knocks to save a new pattern. Once the pattern is recorded, it is saved to NVS memory and the system goes back to main system as shown in [Figure 4.12](#sw-flow-isr).

<div id="sw-flow-isr" align="center">
<figure>
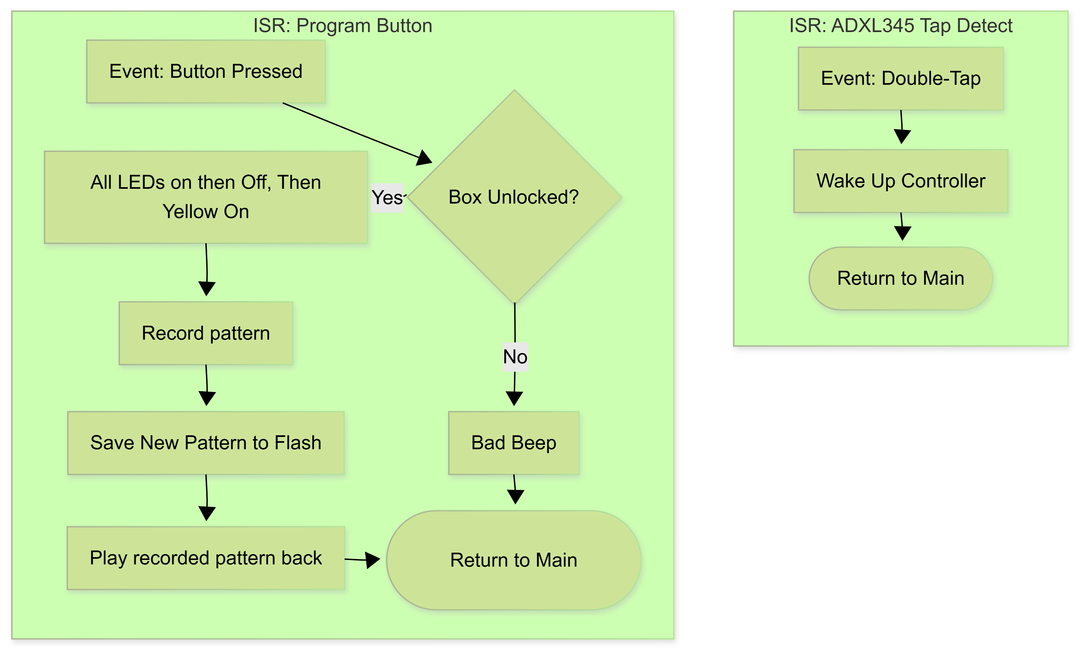
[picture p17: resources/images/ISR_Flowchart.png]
sw-flow
  
  <figcaption align="center"><b>Figure 4.12:</b> Programming Flowchart of Interrupt Service Routines (ISRs)</figcaption>
</figure>
</div>

#### 4.5.2 Code Structure
For easy code understanding and better readability, a modular approach was taken. Splitting the code in different cpp files depending on the type of function. A config.h file also was created to storing all customisability settings. This file had only settings constants and no code or variables to prevent confusion for a user, and make it less error prone. The files structure to be followed is listed in [Table 4.6](#tab:sw-files).

<div style="text-align: left" id="tab:sw-files">

*Table 4.6: Software Files Structure*
| File Name (Header) | Purpose |
|:--- |:--- |
| batteryMonitoring | Functions to monitor battery |
| config | File to store all setting constants, for easy editing of settings |
| globalVariables | File storing all global variables, also explanations of some other important non global variables |
| hardware | All pin, objects definition and hardware initialization and interrupt functions |
| hmi | All human interface related functions, for controlling buzzer, LEDs and actuator |
| KnockLock (ino) | Main code to run with setup and endless loop | 
| patternRecognitionandRecording  | Core functions to process/record |
| sleepMode | Function related to sleep and wake up of controller |
| usingNVS | Functions related to saving and reading data from the non-volatile storage of the controller |
</div>

Arduino IDE is used to program the controller in C++. This is because Arduino IDE provides access to wide range of libraries for various controllers with ease.

The final code implementation can be seen in [Section 5.5](#55-software-implementation).

### 4.6 Housing Design <!-- design for housing -->

<div id="housing-model"  align="center">
  <figure>
  <table border="0">
    <tr>
      <td><figure>
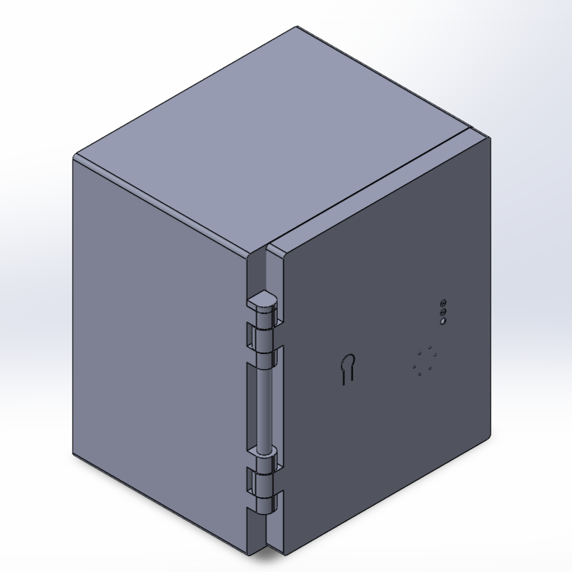
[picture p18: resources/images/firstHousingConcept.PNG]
        
        <figcaption align="center"><b>(a):</b> Closed </figcaption>
      </figure></td>
      <td><figure>
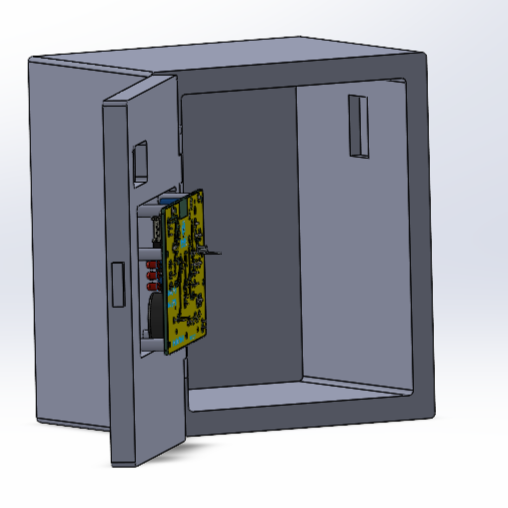
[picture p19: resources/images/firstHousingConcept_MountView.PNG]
        
        <figcaption align="center"><b>(b):</b> Open </figcaption>
      </figure></td>
    </tr>
  </table>
  <figcaption align="center"><b>Figure 4.13:</b>Preliminary 3D Model of Housing</figcaption>
  </figure>
</div>

For demonstration purposes, a box was modeled. The door must mount the PCB, this way the knocks can be reliably detected when door (typically primary place for knocking) is knocked. Many screw pillars have been used for a more firm housing and preventing the PCB from vibrating on its own by making it more rigidly connected with the door. An indent was made in the door to sit the servo motor, and a groove in the housing to slot in the servo to lock the box as shown in [Figure 4.13](#housing-model). Hole have been created in the door to show the LEDs for status of the box and holes on top of the buzzer to allow for better audibility.

The final housing can be seen in [Section 5.6](#56-housing-prototype).

### 4.7 Pre-Implementation Verification Methods <!-- How did we test during development? -->
Since this project follows the V-model design flow, the different layers and aspects of the design must be verified both before and after implementation. The following sections define the test specifications followed to continuously verify and prototype the layers of the design before the system was fully implemented. 

#### 4.7.1 Concept Feasibility Testing <!-- Testing the sensor to see if concept is feasible -->
Before implementation, the feasibility of the knock detection concept must be tested. If there is no reliable way of detecting knocks and most importantly detecting the knock pattern, then the project is a failure. Fortunately, the experimental setups described for sensor selection in [Section 4.4.2](#442-sensor-sub-system) can provide results that not only identify the most appropriate sensor for the project but also the entire concept feasibility. The results of this experiment are presented in [section 5.1.1](#511-concept-feasibility)

#### 4.7.2 Prototype System Testing <!-- Testing entire system in breadboard -->
After confirming feasibility, the system as described in [Section 4.4.1](#441-full-schematic-design) must also be verified. For ease of setup, development modules were selected to test the overall function of the system as well as initiate software development while the PCB was being manufactured. The following components were used:
- Microcontroller: ESP32-DevKitM-1
- HMI: red, yellow and green LEDs and a piezoelectric buzzer
- Sensor: JOY-IT SEN-MMA8452Q
- Lock Actuator: SG90 servo motor
- Misc: breadboard, resistors, jumper cables

The results of this test are presented in [Section 5.1.2](#512-prototype-system)

#### 4.7.3 Prototype Module Testing <!-- Testing different sections of circuitry to see if PCB layout is good -->
Before the PCB could be designed and manufactured, some of the sub-systems were tested to ensure they could function as designed. The following briefly describes the tests conducted:
- **Lock Actuator Sub-system**: 
  - To ensure the power cut off configuration works, the circuit as defined in [Figure 4.6](#lock-actuator-sch) is constructed on a breadboard using an ESP32-DevKitM-1, a BC547B NPN Transistor, an IRF4905 P-channel MOSFET, SER0050 servo motor and through-hole resistors. Only the decoupling capacitors are neglected as the development board provided stable power. The system is feasible if the servo is operational when the transistor base is high and not operational when the transistor base is low. Results of this test are presented in [Section 5.1.3](#513-lock-actuator-interface-test).
- **Programming Interface Sub-system**: 
  - To ensure that the microcontroller can easily be programmed directly via the UART interface, an Arduino UNO board is used to    program an ESP32-DevKitM-1. Like the ESP32C3, the ESP32MINI found on the ESP32-DevKitM-1 has a UART interface which it can supposedly be programmed via. The Arduino Uno board is essentially used as just a USB-to-UART bridge as the enable pin are connected to ground and the RX and TX pins are connected to the TX and RX pins of the ESP32-DevKitM-1 respectively. The system is feasible if the ESP32 board is recognised by Arduino IDE and a simple program can be flashed. Results of this test are presented in [Section 5.1.4](#514-programming-interface-test). 
- **HMI Sub-system**: 
  - To ensure the HMI is well engineered for human use, the circuit as defined in [Figure 4.9](#hmi-sch) is constructed on a breadboard. This test is essentially done as part of the prototype system test as described in [Section 4.7.2](#472-prototype-system-testing). Results of this test are presented in [Section 5.1.5](#515-hmi-test)

### 4.8 Post-Implementation Verification Methods <!-- How did we test after development?-->
After implementation, the system must again be verified to ensure everything is functioning as specified. The following sections thus define the test specifications used to verify the PCB and final product to ensure it ultimately met the [system requirements](#42-system-requirements).

#### 4.8.1 PCB Module Testing <!-- Checking each sub-system on the PCB -->
After the PCB has been assembled, each sub-system must be tested before the entire system integration is tested. For this reason, various test points are included within the schematic as seen in [Figure 4.2](#schematic). The following describes what each test point is designed to check:
- **Sensor Sub-system**: 
  - Test Point 5: the signal sent by the accelerometer's activity interrupt
  - Test Point 6: the supply voltage of the accelerometer
- **Controller Sub-system**
  - Test Point 3: the I2C communication line for the MCU
- **Power Regulation Sub-system**:
  - Test Point 1: the input voltage from the battery supply
  - Test Point 2: the input voltage from the alternative supply via micro USB
  - Test Point 4: the output voltage of the voltage regulator

The main purpose of these test points is checking if components are receiving the correct power. They also check communication lines between the sensor and MCU for debugging. 

In addition to the test points, some test specifications were defined to test the general functionality of the sub-systems:
- **Sensor Sub-system**: 
  - Can only be tested if controller, programming interface and power regulation sub-systems are functional. See [Section 4.8.2](#482-pcb-system-integration-testing) for test specifications.
- **Lock Actuator Interface Sub-system**: 
  - To test functionality of the this sub-system, the voltage across pins 2 and 3 of the servo connector (J5) and voltage of the base (pin 2) of NPN transistor (Q1) relative to ground can be measured. The sub-system is functional if the connector voltage is high when the base voltage is high and low when the base voltage is low. See [Figure 4.6](#lock-actutator-sch) for pins.
- **Controller Sub-system**: 
  - To test functionality of this sub-system, the MCU is connected to power and the status yellow LED checked. The sub-system is functional if the yellow LED is on when the MCU is powered. This is because the yellow LED is on IO19 which pulled up by default.
- **Programming Interface Sub-system**: 
  - To test the functionality of this sub-system, an external USB-to-UART programmer (or Arduino UNO) is connected to the RX and TX pins, the boot pins are connected together and the the reset button is pressed. If the MCU is recognised by Arduino IDE, the sub-system is functional. 
- **HMI Sub-system**:  
  - Can only be tested if controller, programming interface and power regulation sub-systems are functional. See [Section 4.8.2](#482-pcb-system-integration-testing) for test specifications.
- **Power Regulation Sub-system**: 
  - To test the functionality of this sub-system, the voltage at test point 4 relative to ground is be measured when the battery is connected. If this voltage is 3.3V, the sub-system is functional.

#### 4.8.2 PCB System Integration Testing <!-- Checking if sub-systems integrating together as designed -->
With certainty that the sub-systems are powered and functional, the integration between sub-systems can be tested. The following test specifications to test integration were defined:
- **Reading Serial Data of the Sensor**: 
  - To test the functionality and integration of controller, programming interface and sensor sub-systems, the MCU is flashed with an example program to read the sensor data and print it in the serial monitor. The sub-systems are fully integrated if data appears in the serial monitor and is responsive when the PCB is moved around.
- **Programming the MCU to Blink and Beep**: 
  - To test the functionality and integration of controller, programming interface and HMI sub-systems, the MCU is flashed with an example blink program and example beep program from Arduino IDE (with pins adjusted accordingly). The sub-systems are fully integrated if each LED blinks and the buzzer beeps when programmed to.
- **Programming the MCU to Turn on and Cut Lock Actuator Power**: 
  - To test the functionality and integration of controller, programming interface and lock actuator interface sub-systems, the MCU is flashed with a basic program that brings the IO0 high and the voltage across pins 2 and 3 of the servo connector (J5) is measured.  The sub-systems are fully integrated if the voltage is high when IO0 is high.

It should also be noted that all of these tests also verify the integration of the power regulation sub-system as it provides power to all other sub-systems and they would not function without it. 

The results of these tests are presented in [Section 5.8.2](#582-system-integration-performance).

#### 4.8.3 Complete Product Verification <!-- Checking function of the entire PCB -->
Finally, the integration of the complete system must be tested against the requirements outlined in [Section 4.2](#42-system-requirements). 

The setup for this test is defined as follows:
- The MCU is flashed with the program developed in [Section 5.5](#55-software-implementation).
- The PCB is placed on piece of material which is knocked. 
- The USB-to-UART programmer is connected to the RX and TX pins of the PCB so that the serial monitor can be used for debugging
- The MCU is connected to the battery for power

The criteria for the test being successful are:
1. The system can detect whenever the user knocks on the box.
2. The yellow LED is illuminated when the system is in locked state.
3. The servo motor rotates to unlocked position when the correct pre-defined knock pattern is applied in locked state.
4. The green led is illuminated and the buzzer plays the unlocked sound when the correct pre-defined knock pattern is applied in locked state.
5. The red led is illuminated and the buzzer plays the false pattern sound when the correct pre-defined knock pattern is applied in locked state.
6. The green LED is illuminated when the system is in unlocked state.
7. The system enters programming mode and records knocks when the button is pressed in unlocked state. 
8. The system alerts the user that it has entered programming mode when the button is pressed in unlocked state. 
9. The red led is illuminated and the buzzer plays the false pattern sound when the button is pressed in locked state. 
10. The system changes to unlocked state when the most recent pattern defined in programming mode is applied in locked state.
11. The servo motor rotates to locked position when two knocks are applied in unlocked state. 
12. The system goes into sleep state after 60 seconds of inactivity when in locked state.

Once the PCB is verified, these same test specifications can also be used to verify the fully assembled product when the PCB is connected to the housing designed in [Section 4.6](#46-housing-design). 

The results of these tests are presented in [Section 5.8.3](#583-complete-product-performance).

#### 4.8.4 Power Consumption  <!-- Checking power consumption in active and sleep modes -->
Once the general functionality of the system has been verified, another important characteristic of the system must be investigated: the power consumption. To determine the amount of power consumed by the system and estimate the battery life of the system, the current drawn by the system is measured. To do this, an ammeter is connected in series with the power supply and the battery terminal. The system is tested in different modes and functions so that the current measurements in all cases can be taken. The results of this test are presented in [Section 5.8.4](#584-power-consumption).

### 4.9 Validation Methods  <!-- Are we making the right product? -->
After the product has been verified, it must be validated. Essentially, it must be tested in a way to reveal if it not only meets the [system requirements](#42-system-requirements) but the requirements of the user.

#### 4.9.1 User Acceptance Testing  <!-- Presenting prototype to potential users -->
The most direct way to checking the product against the needs of the user is to survey users directly. Over the course of a week, 10 people were surveyed using convenience sampling. Each person was shown the final prototype and asked four questions:
1. What would you rate this product out of ten?
2. What is one feature you especially liked about the product?
3. What is one feature you disliked about the product?
4. What is one feature you believe would improve or should be implemented into the product?

Participants were also allowed to leave any question unanswered. 

The findings can be found in [Section 5.9.1](#591-user-feedback).
<!--------------------------------------------------------------------------------------------------------------------->
<!--------------------------------------------------------------------------------------------------------------------->
## 5	Results
After the entire methodology and intended design were defined, implementation, verification and validation of the system could commence. The results of this phase of the development process are discussed in this section, starting with the prototyping and continuous verification done before the PCB was manufactured.

### 5.1 Pre-Implementation Verification Results
Before the PCB could be designed and manufactured, the system must be verified from concept to the individual sub-systems.

#### 5.1.1 Concept Feasibility 
To verify the feasibility of knock pattern detection, the tests described in [Section 4.4.2 Sensor Sub-system](#442-sensor-sub-system) were conducted and the results are summarized below:
- Both the piezo disc and IMU were able to detect knocks through a plastic case quite reliably. Though, through the wood, only the IMU was able to detect any knocks.
- In both setups, the IMU was able to detect very fast knocks, but the piezo in plastic setup occasionally missed knocks that were too quick. 

Even after trying to make the piezo a more sensitive by using 3.3V supply instead of 5V, it still couldn’t match the performance of the IMU. This result was unexpected considering other projects in the [Literature Review](#2literature-review). Additionally, the I2C communication of the IMU was observed to be significantly more reliable than the voltage output of the piezo element. 

The IMU also gave data for all three axes. A typical series of knocks as detected by the IMU can be seen in [Figure 5.1](#imu-test). The y-axis is the magnitude in g (gravitational units), while the x-axis is time in milliseconds. The blue, yellow and green lines are the x, y and z axis respectively. Each knock caused a peak in each of the three axes, but most prominently in the axis perpendicular to the surface of the material. As such the knock detection software as discussed in [Section 5.5.2](#552knock-detection), initially considered only the value of this axis. [Figure 5.1](#imu-test) also clearly shows that the peaks have a noticeable time gap between them. This suggests that if the peaks are registered as knocks and the interval between peaks are measured, it is definitely feasible for the software to detect a specific knock pattern based on the the amount of knocks and their intervals.

<div id="imu-test" align="center">
<figure>
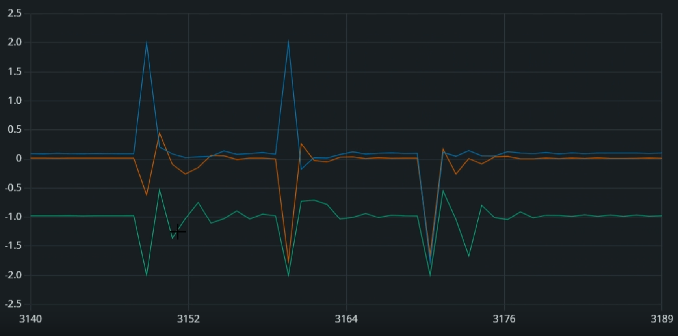
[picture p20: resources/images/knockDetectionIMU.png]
imu-test
  
  <figcaption align="center"><b>Figure 5.1:</b> Serial Plot from Test of MMA8452Q IMU </figcaption>
</figure>
</div>

#### 5.1.2 Prototype System 
With feasibility confirmed, the development processes continued and a prototype for the entire system as described in [Section 4.7.2](#472-prototype-system-testing) was created. The prototype is shown in [Figure 5.2](#system-prototype). 

<div id="system-prototype" align="center">
<figure>
  system-prototype
  <figcaption align="center"><b>Figure 5.2:</b> Breadboard Prototype System</figcaption>
</figure>
</div>

With this prototype, the system was able to recognise knock patterns and alert the user of a successful recognition by turning on the green LED and playing an unlocked sound on the buzzer. Programming mode was also tested as when the button was pushed the system entered programming mode. In this mode, a new knock pattern was applied and the system was reset. Applying this new knock pattern was also recognised after some attempts, and the system played the unlock sound and turned on the green LED. This shows that the system is certainly possible to implement.

However, this prototype had somewhat unreliable knock detection. It was overly sensitive as any movement of the plastic surface was registered as a knock. On the other hand, when the surface was secured to a desk and the desk was knocked, nothing was registered. Many times, the correct knock pattern would also not be recognised. Thus, the system implementation required that great care be taken when designing the surface on which the PCB would be secured (See [Section 5.6](#56-housing-prototype)) and the way the knocking is detected (See [Section 5.5.2](#552-knock-detection)). 

#### 5.1.3 Lock Actuator Interface Test
With the system concept verified, the sub-systems could now be tested and prototyped, starting with the lock actuator interface. The prototype setup is shown in [Figure 5.3](#lock-actuator-prototype). 

<div id="lock-actuator-prototype" align="center">
<figure>
  lock-actuator-prototype
  <figcaption align="center"><b>Figure 5.3:</b> Breadboard Prototype Lock Actuator Interface</figcaption>
</figure>
</div>

In this prototype, an example program to make the servo motor move back and forth continuously was modified so that the pin connected to the base of the NPN transistor (GPIO9) was high. After flashing, the servo rotated as programmed to, indicating that the system was working in on-mode. The program was then modified again so that GPIO9 was low, essentially deactivating the transistor and by extension cutting the servo's supply. After flashing, the servo no longer rotated, indicating that the cut-off worked. To verify again, the voltage between the power line of the servo and ground was measured to be near zero (with a very small leakage of a few mV). Thus, the lock actuator sub-system is feasible as designed.

#### 5.1.4 Programming Interface Test
The next sub-system verified was the programming interface. The setup to test the direct UART programming is shown in [Figure 5.4](#prog-interface-prototype). 

<div id="prog-interface-prototype" align="center">
<figure>
  prog-interface-prototype
  <figcaption align="center"><b>Figure 5.4:</b> Setup to Test Direct UART Programming</figcaption>
</figure>
</div>

When the circuit was setup and the Arduino UNO was connected to the computer, Arduino IDE did not recognise that board was attached. Even after the board was but into UART download mode by holding the boot button and pressing the reset button, the IDE did not detect the ESP32 board, much less allow for flashing. At first, this result seemed to suggest that programming directly via UART was not possible. However, the project team continued testing with different boards (Arduino UNO R4 Wifi, ESP8266 DevKit) and eventually, a AYWHP CP2102 HW-598 USB-UART-TTL converter was purchased. 

The AYWHP CP2102 HW-598 is a USB-to-UART programmer which can connect directly to the RX, TX, VCC and GND pins of the ESP32 board. When connected, put int UART download mode and plugged into the computer, Arduino IDE detected the board immediately. After this success, the ESP32 board was programmed to make the on-board LED blink and it functioned correctly. Thus, the programming interface sub-system is feasible as designed as long as an dedicated USB-to-UART programmer module is used.

#### 5.1.5 HMI Test
The final sub-system prototyped was the HMI. This prototype was done as part of the system prototype shown in [Figure 5.2](#system-prototype). 

When the system was tested, the HMI was programmed to indicate four main actions:
1. Successful unlock
2. Unsuccessful unlock
3. Entering programming mode
4. Successful lock (re-locking the box after unlocking it)

For a successful unlock, the green LED illuminated and the buzzer made an unlock sound. This sound was designed to sound pleasant using two high frequency chirps. Both the project team and other students in the lab at the time of testing found this sound to be pleasant and a good indication that the box has been unlocked.

For an unsuccessful unlock, the red LED illuminated and the buzzer made an alarm sound. This sound was designed to sound unpleasant to deter unauthorised users from tampering with the box. It takes inspiration from the "wrong-choice" buzzer sound featured in many game shows.

For entering programming mode upon the button press, all LEDs flash for a moment before the yellow LED was illuminated to indicate that programming mode has begun recording. 

For successful lock, all of the LEDs turn off for a moment and the yellow LED is illuminated to indicate that the box is locked once again. It should also be noted that the input for re-locking the box is two simple knocks with any interval between. This was done so that the user does not have to remember any complex pattern to re-lock the box and so that accidental re-locking is less likely as opposed to using a single knock.

Overall, the HMI was satisfactorily ergonomic and the sub-system is feasible as designed. A more complete list of the inputs and outputs of the system is provided in [Section 4.4.6](#446-human-machine-interface-sub-system).

### 5.2 Component Selection <!-- Results of tests between components -->
With the system and sub-systems verified, components could be selected according to the specifications outlined in [Section 4.4.8](#448-component-specifications).

#### 5.2.1 Sensor Selection <!-- Choosing an appropriate sensor -->
As demonstrated in [Section 5.1.1](#511-concept-feasibility), the accelerometer exhibited much better performance than the piezo disc and thus the project team decided that an accelerometer would be the most appropriate sensor. 

While the tests were conducted with a MMA8452Q by Sparksfun Electronics, the final design uses an ADXL345, as it was cheaper and larger in package size making it easier to solder. The ADXL345 is also 13-bit instead of 12-bit, hence should perform even better. It also has a very low power consumption (~23uA) [5] making it ideal for project.

#### 5.2.2 Other Components
Aside from the sensors, all components were chosen based on the specifications outlined in [Section 4.4.8](#448-component-specifications) in [Table 4.4](#tabSpecs). The complete list of all materials used is shown in [Section 5.7](#57-bill-of-materials). Any modifications to the components selected or designed in [Section 4](#4methodology-and-design) is explained in following sections. 

### 5.3 PCB Design <!-- PCB layout, issues and changes to schematic -->
With components selected and the system prototype verified, the layout of the PCB could be designed.

#### 5.3.1 PCB Version 1
The first version of the PCB layout is shown in [Figure 5.5](#pcb-v1). In creating the design, a few important things were considered as follows:
- The voltage regulator was placed far away from the MCU to prevent the switching magnetic field from interfering with the processing.
- The track width for power (0.7mm) was significantly larger than that of signals (0.2mm) to ensure power tracks have lower resistance and can carry sufficient current.
- Both the top and bottom copper layers had a ground plane for better grounding and heat dissipation.
- Wherever possible, power and signal tracks were not run parallel to each other.
- Tracks were never drawn with 90 degree bends.

<div id="pcb-v1" align="center">
<figure>
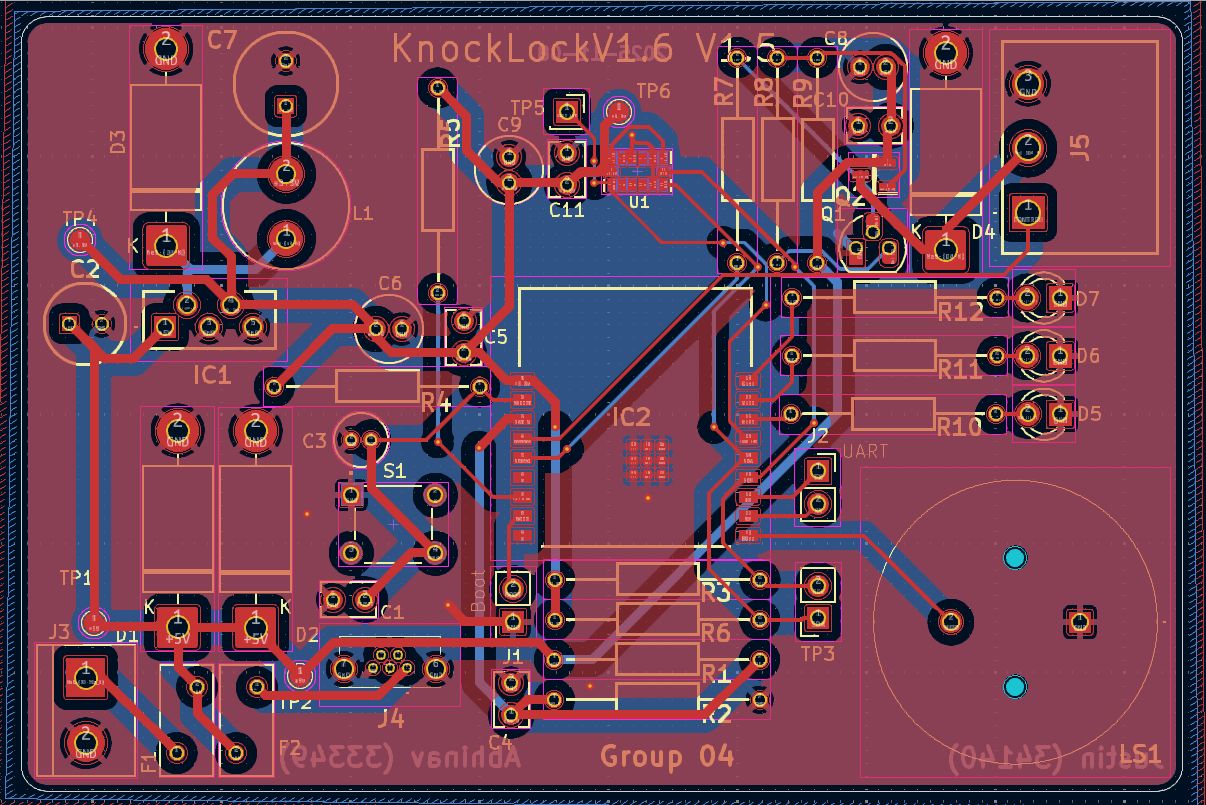
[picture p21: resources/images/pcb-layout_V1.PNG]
pcb-v1
  
  <figcaption align="center"><b>Figure 5.5:</b> First PCB Layout </figcaption>
</figure>
</div>

While this design passed the design rule check in KiCAD, it had a number of issues:
- The biggest issue is that the PCB antenna is above a copper plane which can lead to electromagnetic interference in the ground net.
- Some of the clearances between tracks are too small leading to poor manufacturability and poor insulation between tracks
- 0.2mm track width is difficult to manufacture
- Vias with 0.6mm diameter and 0.3mm hole diameter are too small to be manufactured by AISLER

#### 5.3.2 PCB Version 2
Thus, considering these issues a second design was done as shown in [Figure 5.6](#pcb-v2). In this design, the MCU was shifted to the edge of the PCB and a copper keep-out zone was defined beneath the antenna. The track width and vias diameter were increased to 0.7mm and 0.8mm (with 0.4mm hole diameter) respectively. Additionally, under the advice of Professor Andy Stamm, all of the resistors and ceramic capacitors were changed to surface mount technology (SMT) components instead of through-hole technology (THT) components. The idea behind this switch was that since the accelerometer and MCU required reflow soldering regardless, it would be more efficient to also solder these components in the reflow oven in the same session.

<div id="pcb-v2" align="center">
<figure>
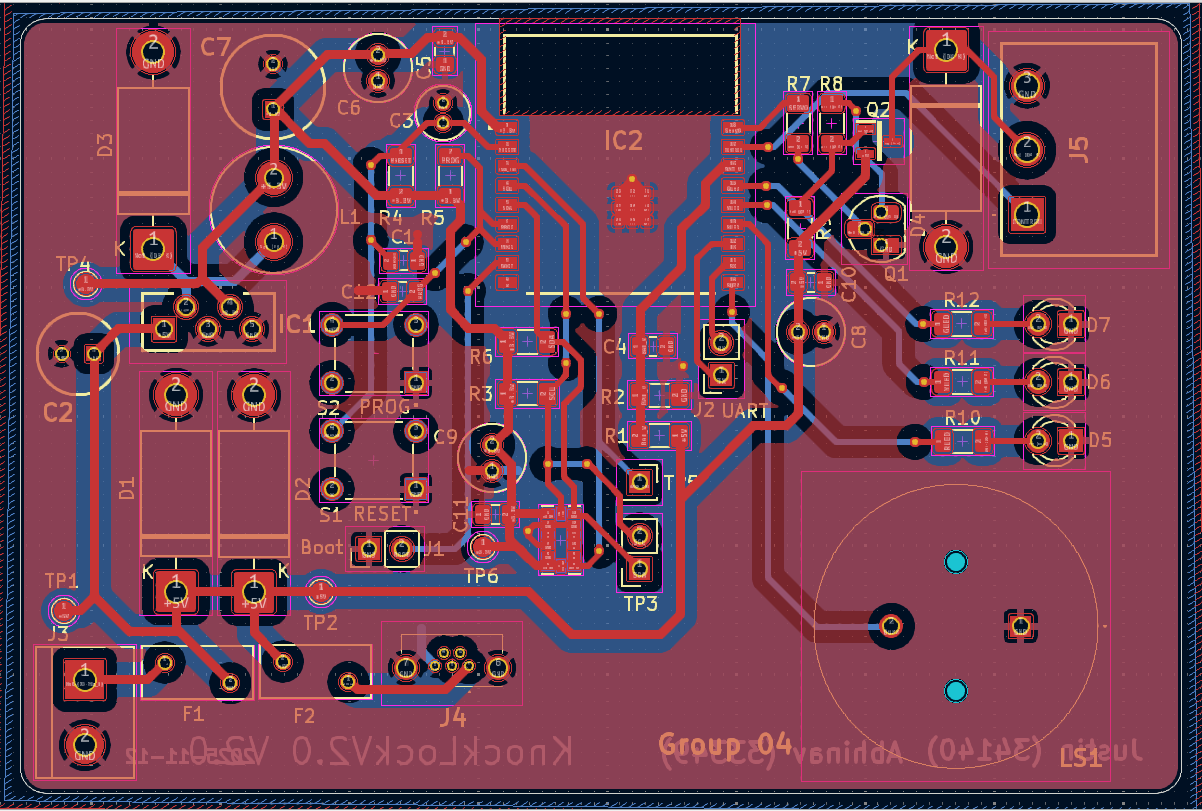
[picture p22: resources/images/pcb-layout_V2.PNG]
pcb-v2
  
  <figcaption align="center"><b>Figure 5.6:</b> Second PCB Layout </figcaption>
</figure>
</div>

In this version of the layout, a button for entering programming mode was also added. For the sake of ergonomics, it was placed on the opposite side of the MCU than the LEDs to ensure that they were fully visible when the button is pressed.

One issue encountered in the formation of this layout was the routing to the micro-controller pins became incredibly difficult. Thus, some of the pins were remapped to make the routing is more intuitive. (Note that the pin mapping in [Table 4.2](#tab:controller-pin-mapping) is already the final mapping).

<div id="tab:pin-revision">

*Table 5.1: Changes in Pin Mapping For PCB Adjustments*
| Signal / Function | Old MCU Pin | New MCU Pin |
| --- | --- | --- |
| Battery Voltage (BAT_V) | 3 | 16 |
| I2C SDA | 14 | 5 |
| I2C SCL | 13 | 4 |
| Wake Interrupt (WAKE_INT) | 15 | 3 |
| Servo Cut-off (SERVO) | 5 | 18 |
| Servo Control Signal | 4 | 17 |
| Red LED | 16 | 13 |
| Yellow LED | 17 | 14 |
| Green LED | 18 | 15 |
</div>

#### 5.3.3 PCB Version 3
Finally, the third and final design shown in [Figure 5.7](#pcb-v3) involved some refinement such changing the battery and servo connectors, adding vias for thermal relief, adding mounting holes and adding a [logo](#logo) in the silkscreen. The change in connectors was to facilitate the use of simple JST pin headers which were available in the lab.

<div id="pcb-v3" align="center">
<figure>
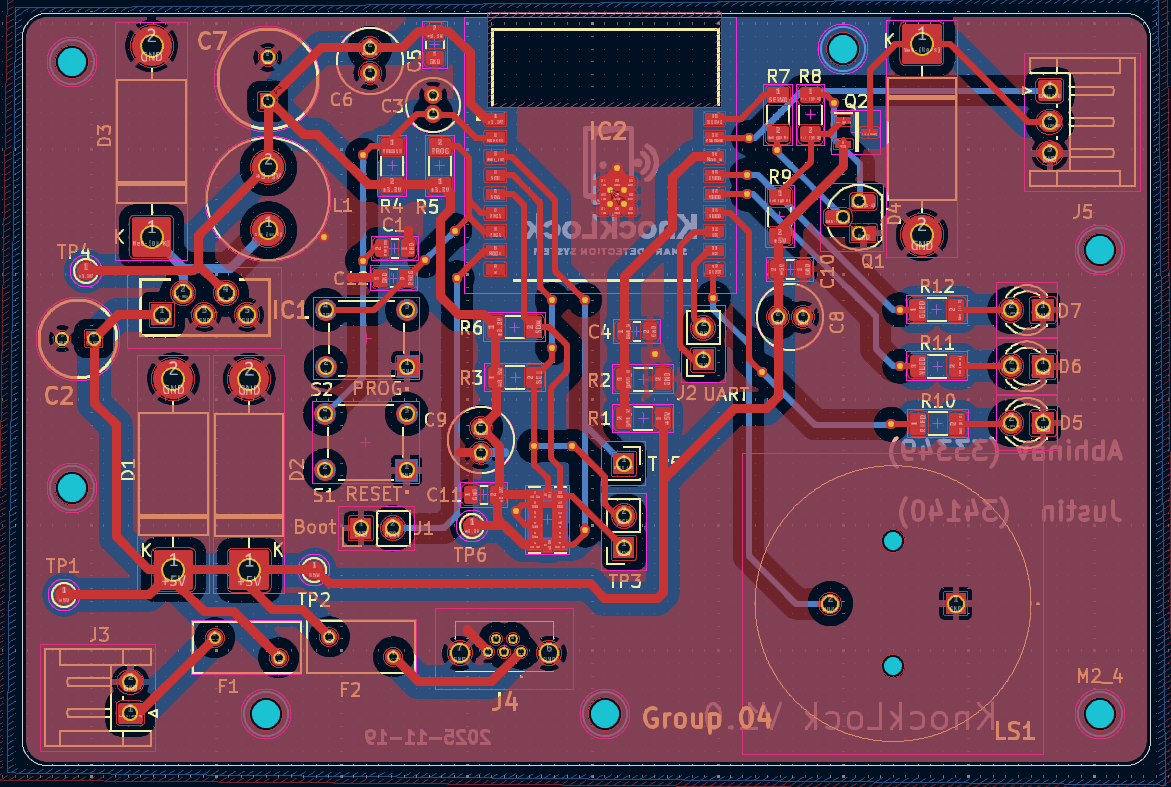
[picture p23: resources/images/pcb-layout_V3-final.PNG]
pcb-v3
  
  <figcaption align="center"><b>Figure 5.7:</b> Final PCB Layout </figcaption>
</figure>
</div>

### 5.4 PCB Assembly <!-- Final and issues encountered in assembly or after testing-->
#### 5.4.1 Assembly Process
After the PCB layout was finalised, the design was sent to AISLER for manufacturing. The final PCB without any components can be seen in [Figure ](#pcb-blank).

<div id="pcb-blank"  align="center">
  <figure>
  <table border="0">
    <tr>
      <td><figure>
        
        <figcaption align="center"><b>(a):</b> Front </figcaption>
      </figure></td>
      <td><figure>
        
        <figcaption align="center"><b>(b):</b> Back </figcaption>
      </figure></td>
    </tr>
  </table>
  <figcaption align="center"><b>Figure 5.8:</b> Final PCB without Components</figcaption>
  </figure>
</div>

Due to the large number of SMT Components, especially the ADXL345 being an LGA (Land Gate Array package), i.e. pads underneath, reflow oven was used to solder those components after placing the components with a pick and place machine. The solder paste was applied manually for each pad with a pneumatic solder paste dispenser. The THT components were later soldered using manual hand soldering.

The fully assembled PCB is shown in [Figure 5.9](#pcb-final).

<div id="pcb-final"  align="center">
  <figure>
  <table border="0">
    <tr>
      <td><figure>
        pcb-front
        <figcaption align="center"><b>(a):</b> Front </figcaption>
      </figure></td>
      <td><figure>
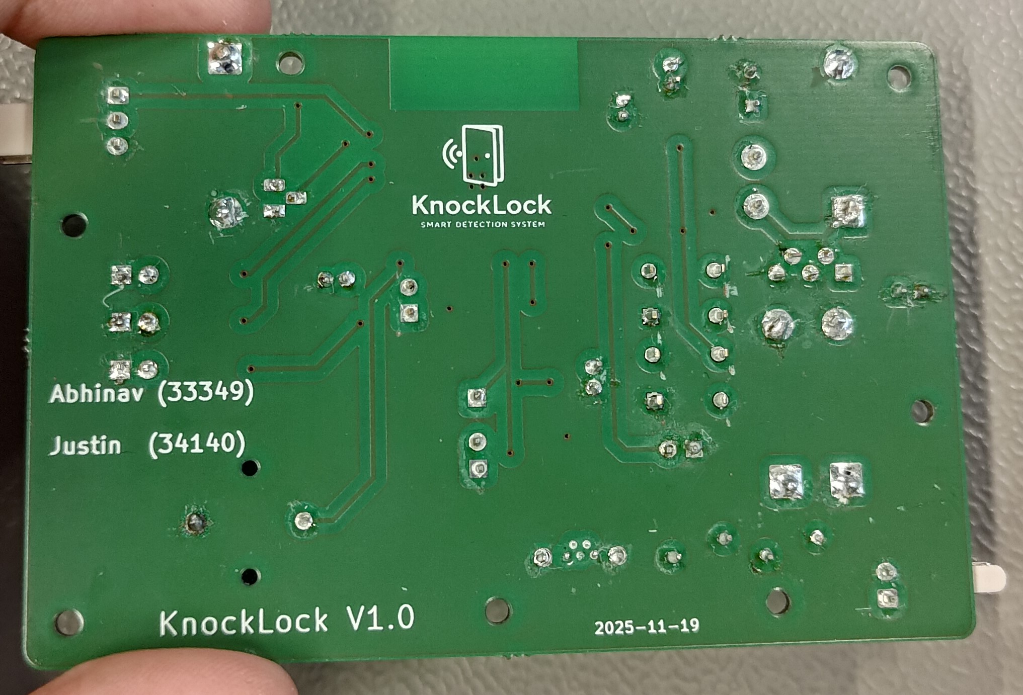
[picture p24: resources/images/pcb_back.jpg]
pcb-back
        
        <figcaption align="center"><b>(b):</b> Back </figcaption>
      </figure></td>
    </tr>
  </table>
  <figcaption align="center"><b>Figure 5.9:</b> Final PCB with Components</figcaption>
  </figure>
</div>

#### 5.4.2 Assembly Issues
Due to the extremely small size of the pads of the ADXL345 pads and ESP32-C3, placing solder paste took many attempts. Only after tweaking the pressure and the nozzle diameter of the dispenser was it possible to place adequate quantities without overfilling the pad. For components such as these, it might be a better approach in future to use a stencil, however for only producing one PCB, the cost of a stencil was not justified and hence the approach avoided. 

Moreover, even though having a large GND plane allowed for better heat dissipation and a better PCB, it made soldering THT components harder as well. Much more heat was required to be able to solder the components reliability. 

Most faults in the soldering were corrected immediately after soldering, due to the continuous [verification process](#48-post-implementation-verification-methods). However one fault was missed. Later during [product validation testing](#491-complete-product-testing), it was discovered the servo was not functioning reliably. After using an oscilloscope to see its response, it was found out that the GND pin of the servo connector was connected, however solder joint was unstable leading to momentary breakage and hence the response was sometimes missed or delayed. This was fixed by soldering it again.

### 5.5 Software Implementation <!-- Final code and issues after testing and how they were solved-->
With the PCB completed, now the software must be implemented on to it, to get the system to work. As discussed in [Section 4.5](#45-software-design) a modular approach was used. The main startup code is in the file KnockLock.ino. 

The libraries used were:
- **ESP32 NVS Library**: For using the NVS memory of ESP32-C3 - in-built with Arduino IDE
- **SparkFun ADXL345 Library (v1.0.0)**: For interfacing with the ADXL345 accelerometer
- **Wire Library**: For I2C communication with the ADXL345 - in-built with Arduino IDE
- **ESP32Servo (v3.0.9)**: For controlling the servo motor

The code implementation of some crucial parts is explained below.
#### 5.5.1 System Initialization
Upon startup, the system must perform many intializations to get everything working correctly in sync. The order is also quite important to save power and to ensure best reliability. 

Upon starting up, its is the important for the system to know why it is starting up. This is because for saving battery, the system is kept in deep-sleep, and in ESP32, waking up from deep-sleep means setup functions runs again. Hence to prevent the system from draining to much battery, even if it woke up to only check battery and alert user for low power or because of double knocking or just first time starting up. How handleWakeup() does this can be seen in [Section 5.5.5](#555-power-management). If the system is supposed to full turn on, only then is the accelerometer setup and the servo enabled. It is important to setupHardware() before checking for wake-up, as the pin must be ready for battery voltage and used to flash the red LED to indicate low battery. setupHardware() is also responsible to attach interrupts to the correct pins and setting up the servo (not enabled yet). How this can be done can be seen in [Listing 1](#lst:setup_hw).

<div id="lst:setup_hw">

*Listing 1: Setting up hardware*
```cpp
if(SERIAL_MONITOR_EN) { // Enable Serial Monitor if required (can be changed in config.h)
    Serial.begin(115200);
    Serial.println("Serial monitor enabled!");
}

setupHardware(); // Setup hardware, all the pins modes and objects

handleWakeup(); //Check reason for waking up, and go accordingly.
// In case of checking battery and flashing led, it only does that and goes back to deep sleep
// If due to double knock, it goes through to normal setup to start listening for knocks

ADXLsetup();                  // Setup ADXL (accelerometer)
digitalWrite(SERVO_EN, HIGH); // Turn servo On
```
</div>

The ADXL, being powered directly by the power regulator (and not the MCU) means it retains its settings hence even in deep-sleep keeps its interrupts and other settings.

Once all hardware is setup, it is important for the system to load back the stored pattern, to prevent having the user from setting up the pattern each time the system wakes up. The system does this by loading the pattern, and its length from the NVS storage on the ESP32. It must then just reset the timers to prevent any unwanted actions before time. The system performs this as shown in [Listing 2](#loadPatternResetTimer).

<div =id"lst:loadPatternResetTimer">

*Listing 2: Loading the pattern and resetting timers*
```cpp
// Load pattern
patternLength = loadPatternFromNVS(targetPattern);

// Reset timers
unsigned long startT = millis();
lastKnockTime = startT;
lastActivityTime = startT;

if(SERIAL_MONITOR_EN) Serial.println("System Ready.");
led_ryg(0, 1, 0);
```
</div>

Both the code snippets above are part of the setup() function in KnockLock.ino file.

For setting up the ADXL (accelerometer), the system uses its library for initializing it with the right settings and then disabling all the unnecessary interrupts. The library used is SparkFun_ADXL345 (Version v1.0.0) as mentioned already in [Section 5.5](#55-software-implementation). All the values are given as constants here, from the setting up in config.h. For giving all these values and communicating with the ADXL, Wire library is used for setting up the I2C communication with it. This allows for easy editing for all parameters from one file. [Listing 3](#init_adxl) from hardware.cpp shows how the ADXL345 is setup.

<div id="init_adxl">

*Listing 3: Setting up the ADXL(accelerometer)*
```cpp
//Function to setup the ADXL sensor with interrupts and sensitivity
void ADXLsetup() {
  Wire.begin(SDA_PIN, SCL_PIN);                                   // Start communication via i2c
  adxl.powerOn();                                                 // Power the ADXL345 on
  adxl.setRangeSetting(SENSITIVITY);                              // Set up the sensitivity, from config.h
  adxl.setTapDetectionOnXYZ(ADXL_EN_X, ADXL_EN_Y, ADXL_EN_Z);     // Enable individual acceleration sensor
  adxl.setTapThreshold(TAP_THRESHOLD);                            // Set minimum threshold for detecting wakeup
  adxl.setTapDuration(TAP_DURATION);                              // Minimum duration for detecting a wake up
  adxl.setDoubleTapLatency(DOUBLE_TAP_LATENCY);                   // Minimum duration between the second tap and first tap
  adxl.setDoubleTapWindow(DOUBLE_TAP_WINDOW);                     // Maximum duration to wait for the second tap
  adxl.singleTapINT(1);                                           // Enable single tap interrupt

  // Disable all other interrupts, until required
  adxl.doubleTapINT(0);
  adxl.FreeFallINT(0);
  adxl.ActivityINT(0);
  adxl.InactivityINT(0);
  adxl.getInterruptSource();        // Reset all interrupt flags 
}
```
</div>

Disabling all interrupts ensure that no unecessary wake-ups occur. Reseting all flags is very important, as ADXL345 interrupts work as latches. Which when triggered keep interrupt high, until reset. 

Now that the system is up and running, it must start detecting knocks.

#### 5.5.2 Knock Detection
When the system is awake, it is in idle state and locked state. During this the system keep checking for battery and the interrupts. Whenever a knock is detected by the ADXL (single tap interrupt) it sets the interrupt pin to high. This triggers an interrupt service routine of the system to set knockDetected as true.

The knock can then be processed and counted to compare against the pattern later. First, as [Listing 4](#readKnocks) shows, it is necessary to prevent a double knock and hence a debounce time is set between two knocks being recorded. Upon a succesful knock, the green LED is flashed, to indicate the knock being detected.

<div id="readKnocks">

*Listing 4: Reading knocks*
```cpp
// Function to deal with response if system locked
void handleLockedState(float aDynamic, unsigned long now) {
  if (knockDetected && (now - lastKnockTime) > DEBOUNCE_TIME) { // If knock is detected start recording its timing, debounce knock to prevent double knock
    lastKnockTime = now;
    lastActivityTime = now; 
    flashGreenTick(); // Alert user a knock was detected
    led_ryg(0, 1, 0); // Show it is still recording
    knockTimes[knockCount] = now;
    knockCount++; // Count number of knocks
    if(SERIAL_MONITOR_EN) Serial.printf("Locked Knock #%d\n", knockCount);
  } else {
    if(digitalRead(YLED) == LOW) digitalWrite(YLED, HIGH);
  }
```
</div>

If it has been long since the last knock, it means the user is done and hence the knock is then checked against the pattern.
The processing of knocks in locked state is shown in [Listing 5](#startCheckingPattern).

<div id="startCheckingPattern">

*Listing 5: Finish reading knocks*
```cpp
  if (knockCount > 0 && (now - lastKnockTime > PATTERN_TIMEOUT)) { // If a long  break with  knocks, start checking the pattern
    checkPattern(); // Check the pattern, if it is correct it goes to unlocked state
    knockCount = 0; // If checked reset for next iteration
    led_ryg(0, 1, 0); // Show it is recording
  }
```
</div>

If no knocks are done, and it has been a while, the system goes to sleep to save battery as shown in [Listing 6](#backToSleep). It also resets its flags at the end to allow system to reuse them in other scenarios.

<div id="backToSleep">

*Listing 6: Going to sleep*
```cpp
  if (knockCount == 0 && (now - lastActivityTime > SLEEP_TIMEOUT)) { // If too long a break with no knocks, go to sleep
    goToSleep();
  }
  knockDetected = false;      // Clear flag
  adxl.getInterruptSource();  // Clear interrupt flags to reset interrupt pin
}
```
</div>

*Issues faced*

Initially a different approach was used for reading and processing the knocks. The raw ADXL values where read continuously while the system is awake and converted to g for easier comparison as shown in [Listing 7](#oldCalcApproach). 

<div id="oldCalcApproach">

*Listing 7: Older magnitude calculation approach*
```cpp
inline float accelMagnitudeG(int x, int y, int z) {
  return sqrt(x*x + y*y + z*z)*0.0039*; // Calculate magnitude, for g, it must be multiplied by 0.0039 (from datasheet) 
}
```
</div>

The result could then be reduced by one to remove the static gravitational force to find dynamic force and compared to a fixed threshold found using many readings. This approach worked, however was not very effective and reliable with it being too sensitive or too insensitive at times. This was later then changed to reading only z-axis (absolute value), keeping in mind the axis is perpendicular to the PCB so when knock a plane parallel to the PCB it was the only axis greatly affected. Same was also seen in [Figure 5.1](#imu-test). This new approach worked much better for detecting knocks, however had one big drawback. It only worked in one specific orientation, with the PCB perpendicular to the ground plane. Finally it was realized, that the wake up which used the double tap interrupt was working much better, and hence for detecting individual knocks, single tap interrupt can be used. As this is made by the developers of the board, its noise removal and reliablitity was extremely high and knocks could be detected in all orientation. The threshold could also be setup much more reliably. The threshold of 40 was set which corresponded to ~2.5g with a measurement sensitivity of 256 LSB/g or 62.5mg/LSB [[5](#9references)]. The system with this threshold was able to ignore most background noise, as well not trigger the system if the box is moved around. (Note the scale +-2g is for reading purposes, and the threshold here is unaffected by it.)

With the new approach, the system is also much more efficient as it is not reading x,y,z values continuously from the ADXL than only reacting to taps. The ADXL is responsible for monitoring the knocks and finding if the knock is above a threshold to be considered a knock, and because the chip is made primarily for that task it is more efficient in doing so.

With the knocks recorded, the system must now check for if the pattern is correct.

#### 5.5.3 Knock Pattern Checking Algorithm
For checking the knock pattern, the system takes a pessimistic approach. Here the pattern is assumed to be wrong , unless proven otherwise. This allows for a safe approach, so that even if the system faces issues, the box is less likely to open. However before checking the pattern, to minimize CPU cycles Some basic checks are done. This helped save processing time, especially if the pattern is completely wrong. The implementation is shown in [Listing 8](#preChecks).
<div id="preChecks">

*Listing 8: Prechecks before checking pattern*
```cpp
// Check if any pattern is even saved, if not return
if (patternLength <= 0) {
    if(SERIAL_MONITOR_EN) Serial.println("⚠ No saved pattern.");
    return;
}

if (knockCount < MIN_KNOCKS)
    return;
```
</div>

These checks were implemented at the start of the function and made sure that if no pattern is saved, or if too few knocks were recorded, the function returns immediately.

If these checks were passed, we calculate the intervals using the knock timings recorded using the code in [Listing 9](#calcIntervals).

<div id="calcIntervals">

*Listing 9: Calculate intervals*
```cpp
// Calculate intervals using knock timings
int intervalCount = knockCount - 1;

for (int i = 1; i < knockCount; i++) {
    intervals[i - 1] = knockTimes[i] - knockTimes[i - 1];
}
```
</div>

The algorithm then checks if the pattern entered by user is too short or too long for the target pattern. This is done, as shown in [Listing 10](#patternLengthCheck), before checking pattern to reduce CPU cycles in case incorrect. It also account for allowed mistake, which can be set from config.h, to make the system a bit more lenient by ignoring a certain number of mistake at the start or the end of the pattern, maybe due to accidental knocks. Setting this to zero makes it only accept only the right pattern of the right length.

<div id="patternLengthCheck">

*Listing 10: Checking pattern length*
```cpp
// Actually checking for mistakes
bool ok = false; // Keep track of a mistake - true means pattern is correct, false means pattern was incorrect
  
// Check for pattern size before actual checking, to be more efficient 
int patternDiff = intervalCount - patternLength; // See difference in the knocks recorded vs knocks to be done
if (patternDiff < 0){
    // Too few knocks 
    ok = false;
    if(SERIAL_MONITOR_EN) Serial.println("Incorrect pattern: Too few knocks");
}
else if (patternDiff > ALLOWED_MISTAKES) {
    // Too many mistakes
    ok = false;
    if(SERIAL_MONITOR_EN) Serial.println("Incorrect pattern: Too many mistakes");
}
```
</div>

If these checks are passed, the system starts checking the pattern, as shown in [Listing 11](#patternChecks), against the stored pattern with a tolerance. This tolerance is necessary, as it is next to impossible to get the exact same timings. Increasing or decreasing this value changes the leniency of the system. The checking also keeps into account the allowed number of mistakes. This is done using a slide window approach, where the pattern is checked against target, if it doesnt match, it is shifted by one until the allowed mistakes and checked against target pattern if correct.

<div id="patternCheck">

*Listing 11: Pattern checking*
```cpp
else {
    for(int mistakeCount = 0; mistakeCount <= patternDiff; mistakeCount++){ 
        // Now if there is a mistake (or multiple), slide window to see if the mistake is at the start only, and full correct pattern is to follow. Run it only till the number of mistakes he has made, which is patternDiff
        bool currentWindowCheck = true; // See if pattern play for a specific window
        for(int k = 0; k < patternLength; k++){
            long diff = labs((long)intervals[k+mistakeCount] - (long)targetPattern[k]);

            if(diff > KNOCK_TOL){ // Is difference not tolerable, according to config.h
              currentWindowCheck = false;
              break; // If a mistake then no need to check rest, go to check if mistake is ignored
            }
        }
        if(currentWindowCheck) { // If pattern is correct after some mistakes (less than allowed mistakes)
            ok = true;
            break;
        }
        else{
            if(mistakeCount == patternDiff) { // Check if it is the last tolerable mistake
                if(SERIAL_MONITOR_EN) Serial.println("Incorrect pattern: Wrong difference");
                break;
            }
        }
    }
}
```
</div>

Then according to the result of the checking stored in the variable ok the system either unlocks the box, sets state to unlocked (hence 1) with a good beep or if ok is false, does a bad beep and goes back to main.

All these code snippers in this section are part of the function checkingPattern() in file patternRecognitionAndRecording.cpp.

Now that the system can check for patterns, it must also be able to store new patterns to check. How this is done is explained in the next [Section 5.5.4](#554-saving-a-new-pattern).

#### 5.5.4 Saving a New Pattern
A similar function to locked state handler was implemented for the unlocked state as well as for recording the knocks to save a pattern. However this can only be called by cliking the programming button (Pin 7) when the box is unlocked. The button is attached as an interrupt, to allow it to be called whenever. Once the pattern was recorded a different function was called to save the pattern to the NVS memory of the ESP32-C3 and also playback the pattern to the user for a confirmation. To do so the the function shown in [Listing 12](#finishRecording) was implemented.

<div id="finishRecording">

*Listing 12: Processing finished recording*
```cpp
void finishRecording() {
  if (knockCount < MIN_KNOCKS) {
    if(SERIAL_MONITOR_EN) Serial.println("❌ Recording Failed: Too few knocks.");
    badBeep();
  } else {
    for (int j = 0; j < knockCount - 1; j++) {
      intervals[j] = knockTimes[j + 1] - knockTimes[j];
    }
    patternLength = knockCount - 1;
    savePatternToNVS(intervals, patternLength);
    successSave();
    playbackPattern();
  }
  currentMode = MODE_IDLE;
  knockCount = 0;
  led_ryg(0, 0, 0); 
}
```
</div>

Here first it is checked if enough knocks were recorded, if not, the user is alerted. If enough knocks were recorded, the intervals are calculated and saved to NVS memory using the function savePatternToNVS(). Then a success indication is given to the user using successSave() function, followed by playback of the pattern using playbackPattern() function. To allow user to unlock the box with the new pattern, without having to reset the system, the stored values are loaded again. They are not loaded each time in checking to save processing time. Finally the system goes back to idle mode, and the knock counts are reset. The LEDs are also turned off, but when it goes back to handle locked or unlocked state, they will be turned on again accordingly.

Finally, the system has all the crucial functions to work. However to run these system it must manage its battery efficiently to last as long as it possible on its battery life.

#### 5.5.5 Power Management
To save power, the ESP32-C3 stays in deep-sleep mode most of the time, only waking up when knocks are detected. However to put the system to sleep appropriate steps must be taken in the correct order. 

Before going to sleep, the system first checks the battery voltage, to see if it is low or not. If it is low, the system must wake up every few seconds to blink the red LED indicating low battery to alert the user to changee it. If the battery is good, the system can sleep indefinitely until a knock is detected. There may be concern, that what if the system does not have low battery when going to sleep, but the battery drains while sleeping. However this is not a really big concern, as the drain will be very slow. Waking it up to check battery status regularly will waste more power. This decision of checking battery only before sleep was taken also taking into account the system has been designed with two sets of power supply, battery and USB. If the battery drains, the user can always plug in the USB power to power the system.

Checking the battery voltage by reading ADC value from the voltage divider and using the formula as stated in [Appendix A](#appendix-a-circuit-dimensioning-calculations-and-formulae). The system compares this to a threshold to denote if it is too low or not, as shown in [Listing 13](#batteryCheck). The system can also start powering down hardware which is not necessary anymore such as the LEDs off (until Red is required later) and the Servo motor.

<div id="batteryCheck">

*Listing 13: Checking battery*
```cpp
led_ryg(0,0,0); // Turn off all LEDs before sleeping
  
// Check Battery before sleeping
float batV = getBatteryVoltage();
bool lowBattery = (batV < LOW_BAT_THRESHOLD_V);

digitalWrite(SERVO_EN, LOW); // Turn servo off the save battery
```
</div>

Now that the system is going to power down, as shown in [Listing 14](#goingToSleep), it is vital to setup a way for it to wake back up, hence the double tap interrupt must be enabled on the ADXL. The GPIO pin connected to this interrupt is then set as wake up GPIO pin, so whenever it is set to high the system wakes up. Hence the system must also disable single tap interrupt to prevent waking up on single taps. The interrupt flags must also be cleared.

Then depending on if battery is low the systems sets up another way of waking back up, using a timer to wake up in regular intervals (60s by default) to flash the red LED to alert user of low battery. After which it again goes back to sleep to save battery.

<div id="goingToSleep">

*Listing 14: Going to sleep*
```cpp
// Prepare ADXL Wakeup
adxl.singleTapINT(0); // No need for single tap interrupt any,ore
adxl.doubleTapINT(1); // Interrupt for double tap on, which wakes up the MCU up
adxl.getInterruptSource(); // Clear the interrupt flags
esp_deep_sleep_enable_gpio_wakeup(1ULL << WAKE_INT, ESP_GPIO_WAKEUP_GPIO_HIGH); // Set the GPU pin connected to interrupt as wake up

if (lowBattery) { // If battery is to low, while sleeping set a timer to wake up and indicate battery status. When battery not low no need to set timer interrupt
    if(SERIAL_MONITOR_EN) Serial.printf("💤 Low Battery (%.2fV). Blinking and sleeping 4s...\n", batV);
    
    // Blink Red indicating "I'm sleeping but dying"
    led_ryg(1,0,0);
    delay(100);
    led_ryg(0,0,0);
    
    // Enable Timer Wakeup
    esp_sleep_enable_timer_wakeup(FLASHING_TIME * 1000000ULL); 
} else {
    if(SERIAL_MONITOR_EN) Serial.println("💤 Good Battery. Deep Sleep (Waiting for Knock)...");
    // No timer wakeup, sleeps indefinitely until knock
}
esp_deep_sleep_start();
```
</div>

As there are two methods of waking up, each with different operations to be performed on wake-up, the wake-up reason is checked and system reacts accordingly as shown in the function in [Listing 15](#handleWakeup)

<div id="handleWakeup">

*Listing 15: Handle Wakeup*
```cpp
// Function to realize reason for wake up, and do tasks accordingly
void handleWakeup(){
  esp_sleep_wakeup_cause_t cause = esp_sleep_get_wakeup_cause();
  if (cause == ESP_SLEEP_WAKEUP_GPIO) {
    // Woke up by ADXL Tap, that means some one wants to get in the box probably
    digitalWrite(YLED, HIGH); 
  } else if (cause == ESP_SLEEP_WAKEUP_TIMER) {
    // Woke up due to low battery, need to indicate using battery
    if(SERIAL_MONITOR_EN) Serial.println("♻ Woke up from Low Bat Timer");
    goToSleep(); // This has the code to check battery status again and indicate led signal accordingly
  }
}
```
</div>

This function must be called near the start of the setup() function (right after Serial setup) to save as much power as possible as previously stated in [Section 5.5.1](#551-system-initialization). The reason for it being in setup() is that after deep-sleep, the ESP32-C3 does a full reset, hence setup() is called again.

As the sytem is in deep-sleep most of the time, when an ESP32-C is woken up from deep-sleep mode, it goes through setup again, and must recall its memory to restore the pattern of the user. To recall these values NVS memory of the controller is used as explained in the next section.
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

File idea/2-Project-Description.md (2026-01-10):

# The Knock Lock
## Problem Statement
As children, many of us might have created special codes that we knock on a door to identify ourselves to our friends or siblings. But, what if those special codes could actually unlock the door itself? 
Better yet, what if you could store your belongings in a safe box which could only be opened if you knock the correct code? 

There are many different types of safes and lock boxes on the market that use systems varying from combinations to NFC, but there are almost no products of this kind that unlocks by recognising a specific 
knocking pattern. As such, the aim of The Knock Lock project is to design and assemble a system that unlocks a lock box by recognizing a specific knocking pattern, perhaps with the hope of extending the idea to work on a full door.

## Requirements
To fully implement the system, a number of requirements related to function, technology and project management have been outlined. 

### Functional Requirements
For Knock Lock Box to be a satisfiable product, the following functional requirements must be implemented:

- It unlocks within 1-2 seconds when a specific knocking pattern is used on the surface of the box
- It turns a green LED on and simultaneously plays a simple beep to indicate that the box has been unlocked
- It rejects pattern if incorrect within 1-2 seconds after knocking has ended
- It turns a red LED on and simultaneously plays a simple alarm to indicate that the knocking pattern was false or unrecognized
- It alerts when the battery level drops below a certain level by flashing a red LED, even in power saving mode
- It only powers on after some initial knock to wake up the system, on wake it shows an yellow LED
- If no knocks detected for 30 seconds, it goes back to power saving mode
- It has provision to use a c port as an alternative power source in case battery dies out, with no prospect to upload firmware through it
- It uses a solenoid to retract or repel the bolt for unlocking and locking respectively

Some further optional and advanced features include:

- It has a programming mode where the user sets the knock for the system to recognize, mode can only be entered when the box is unlocked (for example using NFC)
- It has an NFC to unlock the box in case of system failure
- It alerts user in case door is left unlocked for a long time using beep sound
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

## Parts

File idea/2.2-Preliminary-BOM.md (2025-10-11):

# Preliminary BOM
This is a preliminary parts list. It does not account for all passives (resistors and capacitors) or connectors (wires, solder, pin headers, etc.). Some components are also subject to 
change as design process proceeds. Additionally, any parts that can be found within the University stockpile will be used from there instead of purchased.  
| Qty | Part | Order ID | Vendor | Price [€] |
|-----|---|---|---|---|
| 1 | Piezo contact Sensor | 497-P27040-1 | Mouser | 0.87 |
| 1 | Bleed Resistor (1 MΩ) | 603-RC0805FR-071MP | Mouser | 0.086 |
| 2 | Clamping Diodes | 621-1N4148WT | Mouser | 0.172 |
| 1 | ESP-32 | 356-ESP32C6MINI1H8 | Mouser | 4.69 |
| 1 | N-MOSFET (solenoid driver) | 726-2N7002DWH6327 | Mouser | 0.284 |
| 1 | Solenoid | 485-2776 | Mouser | 4.43 |
| 1 | RGB LED | 941-CMVWQ1B1CBCHBB7A | Mouser | 0.155 |
| 2 | Signal Resistor (1 kΩ) | 603-AF0603FR-071K24L | Mouser | 0.224 |
| 1 | Piezo Buzzer | 179-CPT-2212-3TH | Mouser | 0.79 |
| 1 | Voltage Regulator | 579-MCP1700-3302E/TO | Mouser | 0.43 |
| 2 | Decoupling Capacitors | 81-GRM155D70G475ME5J | Mouser | 0.344 |
| 1 | LiPo Battery | 485-5383 | Mouser | 2.54 |
| 1 | USB C Port (3A IPX7) | 737-USC20SRACS22ESM | Mouser | 1.31 |

Total Price = €17.28
Total Price with VAT = €20.56

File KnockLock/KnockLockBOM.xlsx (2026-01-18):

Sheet: KnockLockBOM
Item Number | Schematic Reference | Qty | Component | Part Number | Manufacturer | Vendor | Price Per Unit | Price
1 | U1 | 1 | Capacitive Accelerometer | ADXL345BCCZ-RL7 | Analog Devices | Mouser | 5.65 | 5.65 | Elect Cost | 26.61 | 15.05 | 11.56
2 | - | 1 | Servo Motor | SG90 | Soldered | HSRW | 5.07 | 5.07 | Mech Cost | 9.7
3 | Q1 | 1 | Bipolar NPN Transistor | BC547B | CDIL | HSRW | 0.04 | 0.04 | PCB Cost | 7.24
4 | Q2 | 1 | P-channel MOSFET | IRLML6402TRPBF | Infineon Technologies | Mouser | 0.35 | 0.35 | Total Cost | 43.55
5 | IC2 | 1 | ESP32 Microcontroller | ESP32-C3-WROOM-02-N4 | Expressif Systems | Mouser | 3.12 | 3.12
6 | D5 | 1 | Red LED | DLE3MMR | Hottech | HSRW | 0.06 | 0.06
7 | D6 | 1 | Yellow LED | DLE3MMY | Hottech | HSRW | 0.06 | 0.06
8 | D7 | 1 | Green LED | DLE3MMG | Hottech | HSRW | 0.06 | 0.06
9 | LS1 | 1 | Buzzer | PKM22EPPH4001-B0 | Murata Electronics | Mouser | 0.48 | 0.48
10 | S1, S2 | 2 | Push Button | TS02-66-60-BK-260-LCR-D | Samesky | Mouser | 0.09 | 0.18
11 | IC1 | 1 | 3.3V Output Voltage Regulator | LM2575-3.3WT | Microchip Technology | Mouser | 1.48 | 1.48
12 | D1,D2 | 2 | TVS Diode | 1N5908 | STMicroelectronics | HSRW | 0.66 | 1.32
13 | D3,D4 | 2 | Schottky Diode | 1N5822 | MIC Electronics | HSRW | 0.15 | 0.3
14 | F1,F2 | 2 | Resettable Fuse | PFRA110 | Schurter | HSRW | 0.28 | 0.56
15 | - | 1 | Battery Holder | 2477 | Keystone Electronics | Mouser | 1.87 | 1.87
16 | - | 4 | AA Battery | - | - | HSRW | 0.3 | 1.2
17 | L1 | 1 | 330uH Inductor | RFC0810B-334KE | Coilcraft | Mouser | 1.26 | 1.26
18 | C1,C4,C5,C10,C11,C12 | 6 | 0.1uF Ceramic Capacitor SMT (0805) | B37873U5101S | EPCOS | HSRW | 0.11 | 0.66
19 | C2 | 1 | 100uF Electrolytic Capacitor | EEU-FC1C101H | Panasonic | HSRW | 0.14 | 0.14
20 | C3 | 1 | 1uF Electrolytic Capacitor | RA1/25-R | Jameco | HSRW | 0.02 | 0.02
21 | C6,C8,C9 | 3 | 10uF Electrolytic Capacitor | EEU-FR1H100 | Panasonic | HSRW | 0.11 | 0.33
22 | C7 | 1 | 330uF Electrolytic Capacitor | EEU-FR1E331 | Panasonic | HSRW | 0.26 | 0.26
23 | J1 | 1 | Male 2 Pin Header | - | - | HSRW | 0.08 | 0.08
24 | J2 | 1 | Female 2 Pin Header | - | - | HSRW | 0.1 | 0.1
25 | J3 | 1 | Male JST 2 Pin Header | - | - | HSRW | 0.1 | 0.1
26 | J4 | 1 | Micro USB B | USB3145-30-1-A | GCT | Mouser | 0.66 | 0.66
27 | J5 | 1 | Male JST 3 Pin Header | - | - | HSRW | 0.12 | 0.12
28 | R1,R4,R5,R7 | 4 | 10kOhms | RC1206FR-0710KL | YAGEO | HSRW | 0.09 | 0.36
29 | R2 | 1 | 6.8kOhms | RC1206FR-076K8L | YAGEO | HSRW | 0.09 | 0.09
30 | R3,R6 | 2 | 4k7Ohms | RC1206FR-074K7L | YAGEO | HSRW | 0.09 | 0.18
31 | R8 | 1 | 100 Ohms | RC1206FR-07100RL | YAGEO | HSRW | 0.09 | 0.09
32 | R9 | 1 | 100kOhms | RC1206FR-07100KL | YAGEO | HSRW | 0.09 | 0.09
33 | R10,R11,R12 | 3 | 27 Ohms | RC1206FR-0727RL | YAGEO | HSRW | 0.09 | 0.27
Item Number |  | Qty | Component | Price Per Unit | Price
35 |  | 7 | M2x6 Screw | 0.11 | 0.77
36 |  | 2 | M2x20 Screw | 0.14 | 0.28
37 |  | 1 | M3x15 Plastic Screw | 0.08 | 0.08
38 |  | 7 | M3 Plastic Washer | 0.01 | 0.07
39 |  | 1 | M3 Hex Nut | 0.07 | 0.07
40 |  | 1 | 3D Printed Housing | 8.43 | 8.43

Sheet: BOM-for-PPT
Component | Comment | Price
Capacitive Accelerometer | ADXL345BCCZ-RL7 | 5.65 | Elect | 26.61
Servo Motor | SG90 | 5.07
ESP32 Microcontroller | ESP32-C3-WROOM-02-N4 | 3.12
HMI | 3 LEDs, Buzzer, Buttons | 0.84
Voltage Regulator | LM2575-3.3WT | 1.48
Power Protection | Diodes, resettable fuses | 1.88
Power Supply | Batteries and Battery holder | 3.07
Electronic Misc | Semi-conductors, Passives, Connectors | 5.5
PCB | PCB from AISLER | 7.24
Housing | 3D Printed Housing, Screws | 9.7
 |  | 43.55

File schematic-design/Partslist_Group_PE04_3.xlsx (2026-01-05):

Group no. |  | 04 |  |  |  | Project | Knock Lock
Date |  | 2025-05-01 |  |  |  | Team members | Justin Chin Cheong, Abhinav Kothari
No. | Qty. | manufacturer | component | ordering code (manufacturer) | vendor | ordering code (vendor) | Price per unit €* | Price €* | Link
1 | 2 | Eagle Plastic Devices (https://www.mouser.de/manufacturer/eagleplasticdevices/) | 12BH342A-GR Battery Holder | 12BH342A-GR | Mouser | 12BH342A-GR | 1.54 | 3.08 | https://www.mouser.de/ProductDetail/Eagle-Plastic-Devices/12BH342A-GR?qs=GYzcNiWpw3fGsZG%2F3838jw%3D%3D
2 | 2 | Microchip Technology | LM2575-3.3WT Voltage Regulator | LM2575-3.3WT | Mouser | 998-LM2575-3.3WT | 1.48 | 2.96 | https://www.mouser.de/ProductDetail/Microchip-Technology/LM2575-3.3WT?qs=kh6iOki%2FeLFAZSEMjMNbiQ%3D%3D
3 | 2 | GCT | USB3145-30-1-A | USB3145-30-1-A | Mouser | 640-USB3145-30-1-A | 0.66 | 1.32 | https://www.mouser.de/ProductDetail/GCT/USB3145-30-1-A?qs=KUoIvG%2F9IlYD1lvSRu5iyg%3D%3D
4 | 2 | Infineon Technologies | IRLML6402TRPBF MOSFET | IRLML6402TRPBF | Mouser | 942-IRLML6402TRPBF | 0.35 | 0.71 | https://www.mouser.de/ProductDetail/Infineon-Technologies/IRLML6402TRPBF?qs=9%252BKlkBgLFf0HuZuONx2Ewg%3D%3D
5 | 4 | MIC | Schottky diode, DO201AD, 40 V, 3 A | 1N5822 | Reichelt | 1N 5822 | 0.15 | 0.60 | https://www.reichelt.com/de/en/shop/product/schottky_diode_do201ad_40_v_3_a-41852
6 | 2 | DFRobot | SER0050 Servo Motor | SER0050 | Mouser | 426-SER0050 | 5.16 | 10.32 | https://www.mouser.de/ProductDetail/DFRobot/SER0050?qs=zW32dvEIR3t5syqsDiJx%2Fw%3D%3D
7 | 4 | Same Sky | Push Button TS02-66-60-BK-260-LCR-D | TS02-66-60-BK-260-LCR-D | Mouser | 179-TS026660BK260LCR | 0.09 | 0.34 | https://www.mouser.de/ProductDetail/Same-Sky/TS02-66-60-BK-260-LCR-D?qs=A6eO%252BMLsxmQnLv1ZYEDDrQ%3D%3D
8 | 2 | Coilcraft | 330 uH Inductor | RFC0810B-334KE | Mouser | 994-RFC0810B-334KE | 1.26 | 2.52 | https://www.mouser.de/ProductDetail/Coilcraft/RFC0810B-334KE?qs=ZYnrCdKdyedaHxMGgKKlpw%3D%3D
9 | 2 | Expressif Systems | ESP-32 | ESP32-C3-WROOM-02-N4 | Mouser | 356-ESP32C3WROOM02N4 | 3.12 | 6.24 | https://www.mouser.de/ProductDetail/Espressif-Systems/ESP32-C3-WROOM-02-N4?qs=stqOd1AaK7%2FqjTZKEOgfUg%3D%3D
10 | 2 | Analog Devices | ADXL345 Accelerometer | ADXL345BCCZ-RL7 | Mouser | 584-ADXL345BCCZ-R7 | 5.65 | 11.30 | https://www.mouser.de/ProductDetail/Analog-Devices/ADXL345BCCZ-RL7?qs=WIvQP4zGaninp9Gc%252BCsJzQ%3D%3D
11 | 2 | Murata Electronics | PKM22EPPH4001-B0 | PKM22EPPH4001-B0 | Mouser | 81-PKM22EPPH4001-B0 | 0.48 | 0.96 | https://www.mouser.de/ProductDetail/Murata-Electronics/PKM22EPPH4001-B0?qs=flZjIlU0hx2Fke4m2iZ9MA%3D%3D
12
13
14
15
16
17
18
 |  |  |  |  |  | total price* |  | 40.36
List of suitable vendors: |  |  |  |  |  | value added tax (VAT) |  | 7.67
shop |  | language | homepage |  |  | total price inclusive VAT: |  | 48.03
HSRW |  | en | https://ee.hsrw.org/
Mouser |  | en/de | https://www.mouser.de/
Reichelt |  | en/de | https://www.reichelt.de/ |  |  |  | *without value added tax (VAT)
Conrad |  | en/de | https://www.conrad.biz/
Other |  |  | only when absolutely necessary

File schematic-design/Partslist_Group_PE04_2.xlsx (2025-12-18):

Group no. |  | 04 |  |  |  | Project | Knock Lock
Date |  | 19/11/2025 |  |  |  | Team members | Justin Chin Cheong, Abhinav Kothari
No. | Qty. | manufacturer | component | ordering code (manufacturer) | vendor | ordering code (vendor) | Price per unit €* | Price €* | Link
1 | 1 | Eagle Plastic Devices (https://www.mouser.de/manufacturer/eagleplasticdevices/) | 12BH342A-GR Battery Holder | 12BH342A-GR | Mouser | 12BH342A-GR | 1.54 | 1.54 | https://www.mouser.de/ProductDetail/Eagle-Plastic-Devices/12BH342A-GR?qs=GYzcNiWpw3fGsZG%2F3838jw%3D%3D
2 | 1 | Microchip Technology | LM2575-3.3WT Voltage Regulator | LM2575-3.3WT | Mouser | 998-LM2575-3.3WT | 1.48 | 1.48 | https://www.mouser.de/ProductDetail/Microchip-Technology/LM2575-3.3WT?qs=kh6iOki%2FeLFAZSEMjMNbiQ%3D%3D
3 | 1 | GCT | USB3145-30-1-A | USB3145-30-1-A | Mouser | 640-USB3145-30-1-A | 0.66 | 0.66 | https://www.mouser.de/ProductDetail/GCT/USB3145-30-1-A?qs=KUoIvG%2F9IlYD1lvSRu5iyg%3D%3D
4 | 1 | Infineon Technologies | IRLML6402TRPBF MOSFET | IRLML6402TRPBF | Mouser | 942-IRLML6402TRPBF | 0.35 | 0.35 | https://www.mouser.de/ProductDetail/Infineon-Technologies/IRLML6402TRPBF?qs=9%252BKlkBgLFf0HuZuONx2Ewg%3D%3D
5 | 2 | MIC | Schottky diode, DO201AD, 40 V, 3 A | 1N5822 | Reichelt | 1N 5822 | 0.15 | 0.30 | https://www.reichelt.com/de/en/shop/product/schottky_diode_do201ad_40_v_3_a-41852
6 | 1 | DFRobot | SER0050 Servo Motor | SER0050 | Mouser | 426-SER0050 | 5.16 | 5.16 | https://www.mouser.de/ProductDetail/DFRobot/SER0050?qs=zW32dvEIR3t5syqsDiJx%2Fw%3D%3D
7 | 2 | Same Sky | Push Button TS02-66-60-BK-260-LCR-D | TS02-66-60-BK-260-LCR-D | Mouser | 179-TS026660BK260LCR | 0.09 | 0.17 | https://www.mouser.de/ProductDetail/Same-Sky/TS02-66-60-BK-260-LCR-D?qs=A6eO%252BMLsxmQnLv1ZYEDDrQ%3D%3D
8 | 1 | Coilcraft | 330 uH Inductor | RFC0810B-334KE | Mouser | 994-RFC0810B-334KE | 1.26 | 1.26 | https://www.mouser.de/ProductDetail/Coilcraft/RFC0810B-334KE?qs=ZYnrCdKdyedaHxMGgKKlpw%3D%3D
9
10
11
12
13
14
15
16
17
18
 |  |  |  |  |  | total price* |  | 10.93
List of suitable vendors: |  |  |  |  |  | value added tax (VAT) |  | 2.08
shop |  | language | homepage |  |  | total price inclusive VAT: |  | 13.00
HSRW |  | en | https://ee.hsrw.org/
Mouser |  | en/de | https://www.mouser.de/
Reichelt |  | en/de | https://www.reichelt.de/ |  |  |  | *without value added tax (VAT)
Conrad |  | en/de | https://www.conrad.biz/
Other |  |  | only when absolutely necessary

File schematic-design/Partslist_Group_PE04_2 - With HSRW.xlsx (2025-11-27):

Group no. |  | 04 |  |  |  | Project | Knock Lock
Date |  | 23/10/2025 |  |  |  | Team members | Justin Chin Cheong, Abhinav Kothari
No. | Qty. | manufacturer | component | ordering code (manufacturer) | vendor | ordering code (vendor) | Price per unit €* | Price €* | Link
1 | 1 | Expressif Systems | ESP-32 | ESP32-C3-WROOM-02-N4 | Mouser | 356-ESP32C3WROOM02N4 | 3.12 | 3.12 | https://www.mouser.de/ProductDetail/Espressif-Systems/ESP32-C3-WROOM-02-N4?qs=stqOd1AaK7%2FqjTZKEOgfUg%3D%3D
2 | 1 | Analog Devices | ADXL345 Accelerometer | ADXL345BCCZ-RL7 | Mouser | 584-ADXL345BCCZ-R7 | 5.65 | 5.65 | https://www.mouser.de/ProductDetail/Analog-Devices/ADXL345BCCZ-RL7?qs=WIvQP4zGaninp9Gc%252BCsJzQ%3D%3D
3 | 1 | Murata Electronics | PKM22EPPH4001-B0 Buzzer | PKM22EPPH4001-B0 | Mouser | 81-PKM22EPPH4001-B0 | 0.48 | 0.48 | https://www.mouser.de/ProductDetail/Murata-Electronics/PKM22EPPH4001-B0?qs=flZjIlU0hx2Fke4m2iZ9MA%3D%3D
4 | 1 | Keystone Electronics (https://www.mouser.de/manufacturer/keystone/) | 2477 Battery Holder | 2477 | Mouser | 534-2477 | 1.87 | 1.87 | https://www.mouser.de/ProductDetail/Keystone-Electronics/2477?qs=Q3RoVmURDolEbXnNenQutg%3D%3D
5 | 1 | Microchip Technology | LM2575-3.3WT Voltage Regulator | LM2575-3.3WT | Mouser | 998-LM2575-3.3WT | 1.48 | 1.48 | https://www.mouser.de/ProductDetail/Microchip-Technology/LM2575-3.3WT?qs=kh6iOki%2FeLFAZSEMjMNbiQ%3D%3D
6 | 2 | PFRA | Resettable fuse Ihold=1.1A, Itrip=2.2A, trip time 6.6s, max. 40 A, 30 V radial | PFRA 110 | HSRW | 261 | 0.28 | 0.56 | https://www.reichelt.de/de/de/shop/produkt/rueckstellende_sicherungen_max_40a-30v_6_6s-35211
7 | 1 | GCT | USB3145-30-1-A | USB3145-30-1-A | Mouser | 640-USB3145-30-1-A | 0.66 | 0.66 | https://www.mouser.de/ProductDetail/GCT/USB3145-30-1-A?qs=KUoIvG%2F9IlYD1lvSRu5iyg%3D%3D
8 | 1 | Infineon Technologies | IRLML6402TRPBF MOSFET | IRLML6402TRPBF | Mouser | 942-IRLML6402TRPBF | 0.35 | 0.35 | https://www.mouser.de/ProductDetail/Infineon-Technologies/IRLML6402TRPBF?qs=9%252BKlkBgLFf0HuZuONx2Ewg%3D%3D
9 | 1 | CDIL | Bipolartransistor | BC547B | HSRW | 203 | 0.04 | 0.04 | https://www.reichelt.de/de/de/shop/produkt/bipolartransistor_npn_45v_0_1a_0_5w_to-92-5006
10 | 2 | MIC | Schottky diode, DO201AD, 40 V, 3 A | 1N5822 | Reichelt | 1N 5822 | 0.15 | 0.30 | https://www.reichelt.com/de/en/shop/product/schottky_diode_do201ad_40_v_3_a-41852
 | 2 | ST | TVS Diode 5V | 1N5908 | HSRW |  |  |  | https://www.mouser.de/ProductDetail/STMicroelectronics/1N5908?qs=YstF3%2FqpSF%252BhnZj98fb9oQ%3D%3D
11 | 1 | DFRobot | SER0050 Servo Motor | SER0050 | Mouser | 426-SER0050 | 5.16 | 5.16 | https://www.mouser.de/ProductDetail/DFRobot/SER0050?qs=zW32dvEIR3t5syqsDiJx%2Fw%3D%3D
12 | 3 | Panasonic | Electrolytic Capacitor 10uF | EEU-FR1H100 | HSRW | 385 | 0.11 | 0.33 | https://www.mouser.de/ProductDetail/Panasonic/EEU-FR1H100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
13 | 1 | Panasonic | Electrolytic Capacitor 330uF | EEUFR1E331 | HSRW | 409 | 0.26 | 0.26 | https://www.reichelt.de/de/de/shop/produkt/elko_radial_330_f_25_v_105_low_esr_8x11_5_mm_rm_3_5-121265
14 | 1 | Panasonic | Electrolytic Capacitor 100uF | EEU-FC1C101H | HSRW | 397 | 0.14 | 0.14 | https://www.mouser.de/ProductDetail/Panasonic/EEU-FC1C101H?qs=%2FC1U95aQ15szP%252BXx0reJVg%3D%3D
15 | 1 | Panasonic | Electrolytic Capacitor 1uF |  | HSRW | 378 | 0.02 | 0.02 | https://www.reichelt.de/de/de/shop/produkt/subminiatur-elko_radial_1_0_f_63_v_rm_1_5_85_c_1000h_20_-18162
16 | 6 | Epcos | 100nF Ceramic-Chip Capacitors |  | HSRW
17 | 1 | Hottech | Red LED | DLE3MMR | HSRW | 498 | 0.06 | 0.06 | https://www.reichelt.de/de/de/shop/produkt/led_3_mm_bedrahtet_rot_191_mcd_50_-10228
18 | 1 | Hottech | Green LED | DLE3MMG | HSRW | 497 | 0.06 | 0.06 | https://www.reichelt.de/de/de/shop/produkt/led_3_mm_bedrahtet_gruen_74_mcd_38_-10227
19 | 1 | Hottech | Yellow LED | DLE3MMY | HSRW | 471 | 0.06 | 0.06 | https://www.reichelt.de/de/de/shop/produkt/led_3_mm_bedrahtet_gelb_210_mcd_53_-10226
20 | 2 | Same Sky | Push Button TS02-66-60-BK-260-LCR-D | TS02-66-60-BK-260-LCR-D | Mouser | 179-TS026660BK260LCR | 0.09 | 0.17 | https://www.mouser.de/ProductDetail/Same-Sky/TS02-66-60-BK-260-LCR-D?qs=A6eO%252BMLsxmQnLv1ZYEDDrQ%3D%3D
21 | 1 | Coilcraft | 330 uH Inductor | RFC0810B-334KE | Mouser | 994-RFC0810B-334KE | 1.26 | 1.26 | https://www.mouser.de/ProductDetail/Coilcraft/RFC0810B-334KE?qs=ZYnrCdKdyedaHxMGgKKlpw%3D%3D
22
 |  |  |  |  |  | total price* |  | 22.04
List of suitable vendors: |  |  |  |  |  | value added tax (VAT) |  | 4.19
shop |  | language | homepage |  |  | total price inclusive VAT: |  | 26.23
HSRW |  | en | https://ee.hsrw.org/
Mouser |  | en/de | https://www.mouser.de/
Reichelt |  | en/de | https://www.reichelt.de/ |  |  |  | *without value added tax (VAT)
Conrad |  | en/de | https://www.conrad.biz/
Other |  |  | only when absolutely necessary

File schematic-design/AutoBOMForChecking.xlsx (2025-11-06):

Reference | Qty | Value | DNP | Exclude from BOM | Exclude from Board | Footprint | Datasheet | Source | In Partslist
C1 | 1 | 100uF |  |  |  | SamacSys_Parts:CAPPRD250W55D630H1220 | http://industrial.panasonic.com/cdbs/www-data/pdf/RDF0000/ABA0000C1209.pdf
C2 | 1 | 330uF |  |  |  | SamacSys_Parts:CAPPRD350W65D800H1300 | http://industrial.panasonic.com/cdbs/www-data/pdf/RDF0000/ABA0000C1259.pdf
C3,C7,C9 | 3 | 10uF |  |  |  | Capacitor_THT:C_Radial_D5.0mm_H11.0mm_P2.00mm | ~
C4,C5,C6,C8,C10 | 5 | 0.1uF |  |  |  | Capacitor_THT:C_Rect_L4.0mm_W2.5mm_P2.50mm | ~ | Mouser | Y
C11 | 1 | 1uF |  |  |  | Capacitor_THT:C_Radial_D4.0mm_H7.0mm_P1.50mm | ~
D1,D5,D6,D7 | 4 | 1N5822 |  |  |  | Diode_THT:D_DO-201AD_P15.24mm_Horizontal | http://www.vishay.com/docs/88525/1n5817.pdf,http://www.vishay.com/docs/88526/1n5820.pdf | Reichelt | Y
D2 | 1 | R-LED |  |  |  | LED_THT:LED_D3.0mm | ~ | HSRW | Y
D3 | 1 | Y-LED |  |  |  | LED_THT:LED_D3.0mm | ~ | HSRW | Y
D4 | 1 | G-LED |  |  |  | LED_THT:LED_D3.0mm | ~ | HSRW | Y
F1,F2 | 2 | Polyfuse |  |  |  | Fuse:Fuse_BelFuse_0ZRE0012FF_L8.3mm_W3.8mm | ~ | HSRW | Y
IC1 | 1 | ESP32-C3-WROOM-02-N4 |  |  |  | SamacSys_Parts:ESP32C3WROOM02N4 | https://www.mouser.ch/datasheet/2/891/Espressif_ESP32_C3_WROOM_02-2006871.pdf
IC2 | 1 | LM2575-3.3WT |  |  |  | SamacSys_Parts:LM257533WT | https://ww1.microchip.com/downloads/en/DeviceDoc/lm2575.pdf | Mouser | Y
J1 | 1 | Screw_Terminal_01x02 |  |  |  | TerminalBlock:TerminalBlock_bornier-2_P5.08mm | ~
J2 | 1 | USB3145-30-1-A |  |  |  | SamacSys_Parts:USB3145301A | https://gct.co/connector/usb3145 | Mouser | Y
J3 | 1 | TBP04R12-500-03BE |  |  |  | SamacSys_Parts:TBP04R1250003BE | https://www.sameskydevices.com/product/resource/tbp04r12-500.pdf
J4 | 1 | UART |  |  |  | Connector_PinHeader_2.54mm:PinHeader_1x02_P2.54mm_Vertical | ~
J5 | 1 | Boot Pins |  |  |  | Connector_PinHeader_2.54mm:PinHeader_1x02_P2.54mm_Vertical | ~
L1 | 1 | 330uH |  |  |  | Inductor_THT:L_Radial_D9.5mm_P5.00mm_Fastron_07HVP | ~ | Mouser | Y
LS1 | 1 | PKM22EPPH4001-B0 |  |  |  | SamacSys_Parts:PKM22EPPH4001B0 | https://www.murata.com/products/productdata/8801054064670/SPEC-PKM22EPPH4001-B0.pdf?1517839211000
Q1 | 1 | IRLML6402TRPBF |  |  |  | SamacSys_Parts:SOT95P237X112-3N | http://www.infineon.com/dgdl/irlml6402pbf.pdf?fileId=5546d462533600a401535668d5c2263c | Mouser | Y
Q2 | 1 | BC547B |  |  |  | Package_TO_SOT_THT:TO-92_HandSolder | https://www.onsemi.com/pub/Collateral/2N3903-D.PDF
R1,R2 | 2 | 4k7Ohms |  |  |  | SamacSys_Parts:RESAD1590W60L630D240 | ~
R3,R4,R5 | 3 | 27 Ohms |  |  |  | SamacSys_Parts:RESAD1590W60L630D240 | ~
R6,R8,R9,R13 | 4 | 10kOhms |  |  |  | SamacSys_Parts:RESAD1590W60L630D240 | ~
R7 | 1 | 6.8kOhms |  |  |  | SamacSys_Parts:RESAD1590W60L630D240 | ~
R11 | 1 | 100 Ohms |  |  |  | SamacSys_Parts:RESAD1590W60L630D240 | ~
R12 | 1 | 100kOhms |  |  |  | SamacSys_Parts:RESAD1590W60L630D240 | ~
S2 | 1 | TS02-66-60-BK-260-LCR-D |  |  |  | TS02-66-60-BK-260-LCR-D:SW_TS02-66-60-BK-260-LCR-D |  | Mouser | Y
TP1 | 1 | TP_Bat |  |  |  | TestPoint:TestPoint_Pad_D1.5mm | ~
TP2 | 1 | TP_Ext |  |  |  | TestPoint:TestPoint_Pad_D1.5mm | ~
TP3 | 1 | TP_3V3 |  |  |  | TestPoint:TestPoint_Pad_D1.5mm | ~
TP4 | 1 | TP_I2C |  |  |  | Connector_PinHeader_2.54mm:PinHeader_1x02_P2.54mm_Vertical | ~
TP5 | 1 | TP_IMUV |  |  |  | TestPoint:TestPoint_Pad_D1.5mm | ~
TP6 | 1 | TP_IMUINT |  |  |  | Connector_PinSocket_2.54mm:PinSocket_1x01_P2.54mm_Vertical | ~
U1 | 1 | ADXL345BCCZ-RL7 |  |  |  | ADXL345BCCZ-RL7:PQFN80P500X300X100-14N |  | Mouser | Y

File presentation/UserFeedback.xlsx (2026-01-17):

User Feedback
S. No. | Overall Rating (Out of 10) | Good feature | Bad Feature | Lacking feature/Potential improvements
1 | 9 | Keyless entry | Knocking anywhere | Only possibility to store one password
2 | 9 | Keyless entry | Electronics too visisble | -
3 | 9 | Asleep when not in use | Not safe as knock could be heared and mimicked | No recovery method
4 | 9 | You can knock anywhere | Knob too small to open | Possibility of mechanical unlocking
5 | 9.5 | Like the idea of beats to unlock | - | Different shapes for housing
6 | 9 | Keyless entry | Housing slides too much | Using rubber pads on bottom of housing
7 | 10 | - | - | -
8 | 9.5 | - | Door can easily be pulled open | No recovery method
9 | 10 | Like the idea of beats to unlock | - | -
10 | 9 | Keyless entry | - | Could be implemented into a mailbox

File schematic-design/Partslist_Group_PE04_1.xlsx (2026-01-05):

Group no. |  | 04 |  |  |  | Project | Knock Lock
Date |  | 23/10/2025 |  |  |  | Team members | Justin Chin Cheong, Abhinav Kothari
No. | Qty. | manufacturer | component | ordering code (manufacturer) | vendor | ordering code (vendor) | Price per unit €* | Price €* | Link
1
2
3
4 |  |  |  |  |  |  |  | 0.00
5 |  |  |  |  |  |  |  | 0.00
6 |  |  |  |  |  |  |  | 0.00
7 |  |  |  |  |  |  |  | 0.00
8 |  |  |  |  |  |  |  | 0.00
9 |  |  |  |  |  |  |  | 0.00
10 |  |  |  |  |  |  |  | 0.00
11 |  |  |  |  |  |  |  | 0.00
12 |  |  |  |  |  |  |  | 0.00
13 |  |  |  |  |  |  |  | 0.00
14 |  |  |  |  |  |  |  | 0.00
15 |  |  |  |  |  |  |  | 0.00
 |  |  |  |  |  | total price* |  | 0.00
List of suitable vendors: |  |  |  |  |  | value added tax (VAT) |  | 0.00
shop |  | language | homepage |  |  | total price inclusive VAT: |  | 0.00
HSRW |  | en | https://ee.hsrw.org/
Mouser |  | en/de | https://www.mouser.de/
Reichelt |  | en/de | https://www.reichelt.de/ |  |  |  | *without value added tax (VAT)
Conrad |  | en/de | https://www.conrad.biz/
Other |  |  | only when absolutely necessary

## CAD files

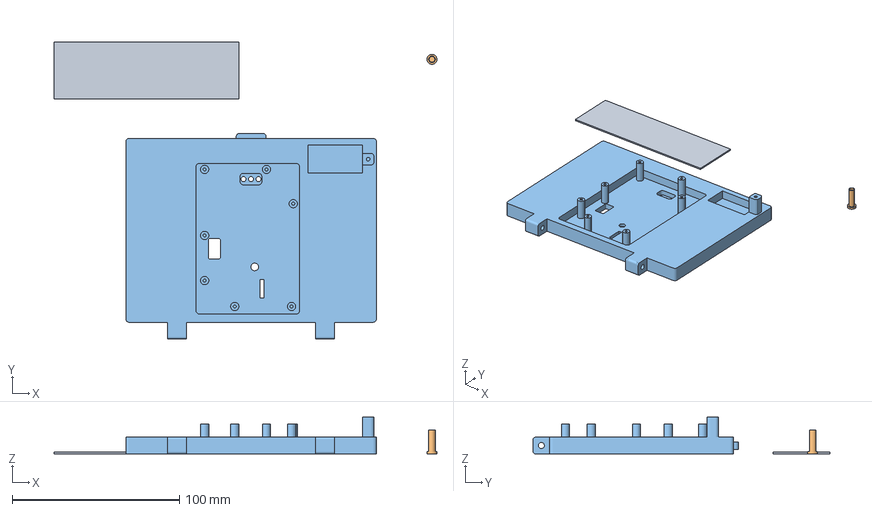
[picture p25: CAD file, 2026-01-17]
3d-design/v4.0/cover_door_button.3mf
229.1 x 177.7 x 22.0 mm
BatteryCover.STL
ButtonPress.STL
KnockLock_Door.STL

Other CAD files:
3d-design/v4.0/KnockLockBox.SLDASM
3d-design/v4.0/KnockLock.SLDASM
3d-design/v4.0/KnockLock_Door.SLDPRT
KnockLock/part-libraries/ADXL345BCCZ-RL7/ADXL345BCCZ-RL7.step
KnockLock/part-libraries/CFR-25JT-52-10K/CFR-25JT-52-10K.stp
KnockLock/part-libraries/CFR-25JT-52-4K7/CFR-25JT-52-4K7.stp
KnockLock/part-libraries/EEU-FC1C101H/EEU-FC1C101H.stp
KnockLock/part-libraries/EEU-FR1E331/EEU-FR1E331.stp
KnockLock/part-libraries/ESP32-C3-WROOM-02-N4/ESP32-C3-WROOM-02-N4.stp
KnockLock/part-libraries/LM2575-3.3WT/LM2575-3.3WT.stp
KnockLock/part-libraries/MC74HC74ADTR2G/MC74HC74ADTR2G.stp
KnockLock/part-libraries/NE555DR/NE555DR.stp
KnockLock/part-libraries/PKM22EPPH4001-B0/PKM22EPPH4001-B0.stp
KnockLock/part-libraries/TS02-66-60-BK-260-LCR-D/TS02-66-60-BK-260-LCR-D.step
KnockLock/part-libraries/UJ20-C-H-G-TH-P16-TR/UJ20-C-H-G-TH-P16-TR.step
3d-design/v4.0/KnockLock_Box_Top.SLDPRT
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

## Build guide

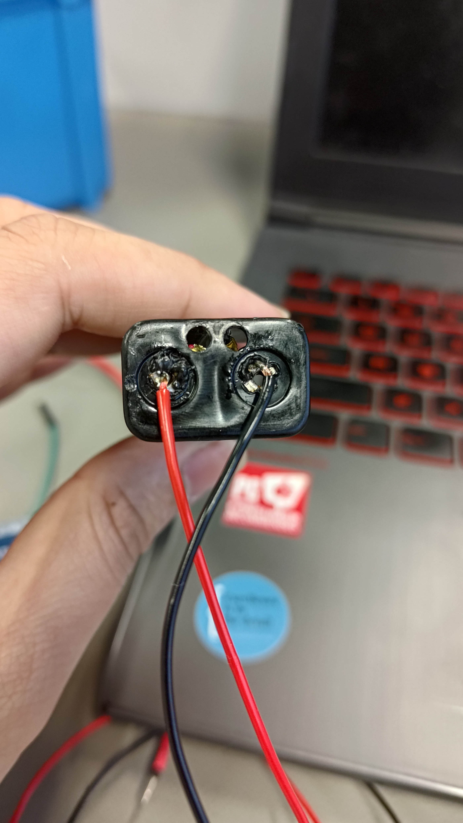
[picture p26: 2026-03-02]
resources/images/battery-holder_resolder.jpg

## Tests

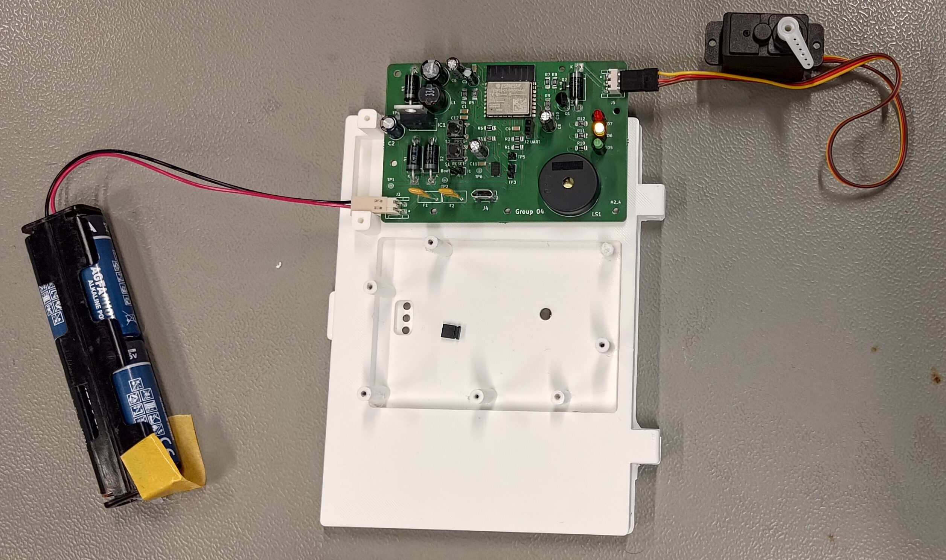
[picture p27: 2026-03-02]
resources/images/pcb-testing-integration.jpg

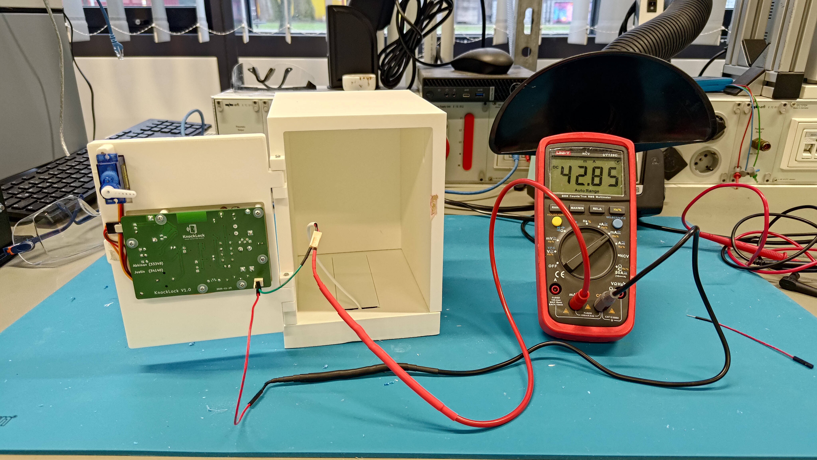
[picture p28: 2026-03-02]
resources/images/power-consumption-verification.jpg

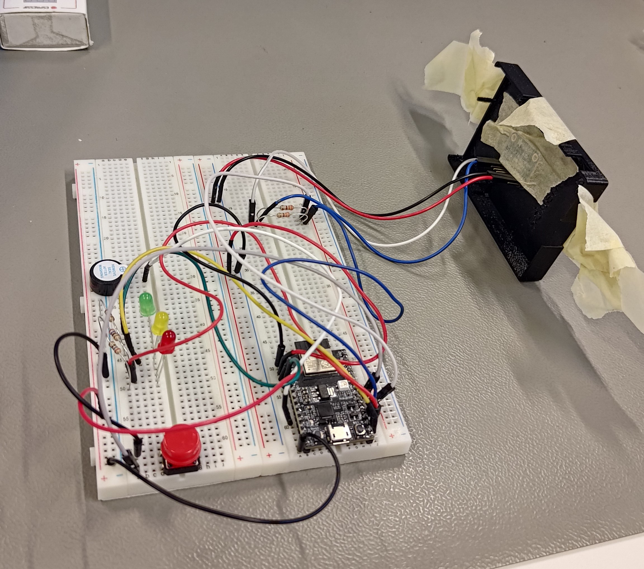
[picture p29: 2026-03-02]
resources/images/testingSystem_iso.jpg

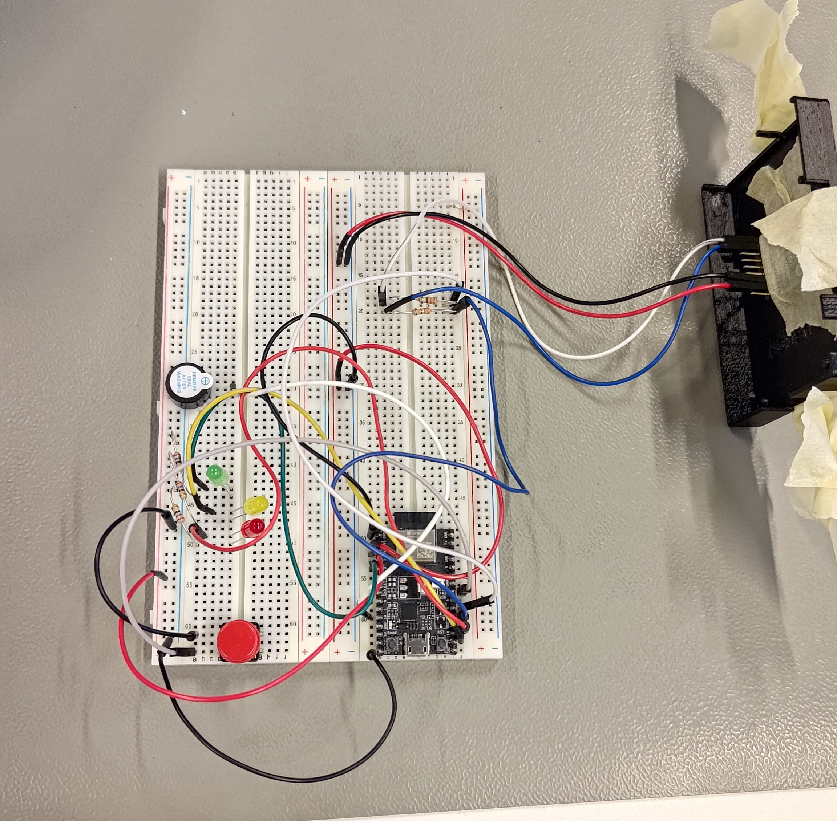
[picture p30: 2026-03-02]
resources/images/testingSystem_top.jpg

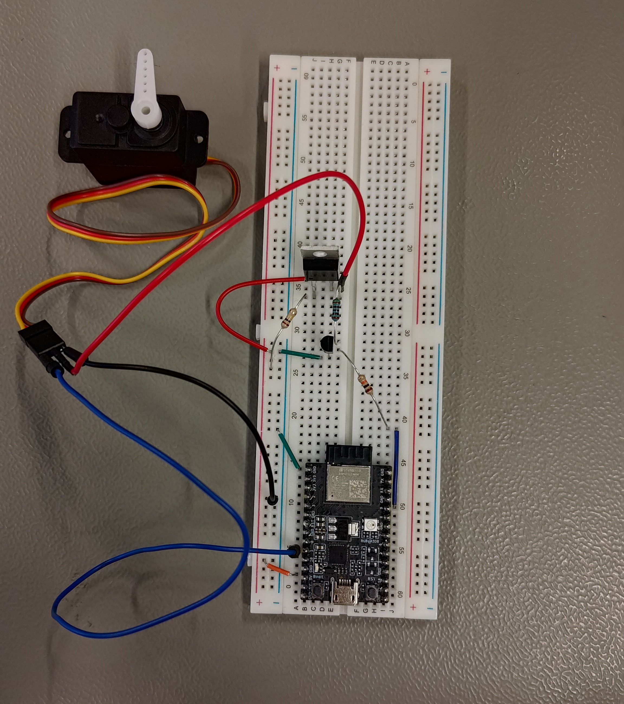
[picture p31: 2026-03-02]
resources/images/motor-control_test.jpg

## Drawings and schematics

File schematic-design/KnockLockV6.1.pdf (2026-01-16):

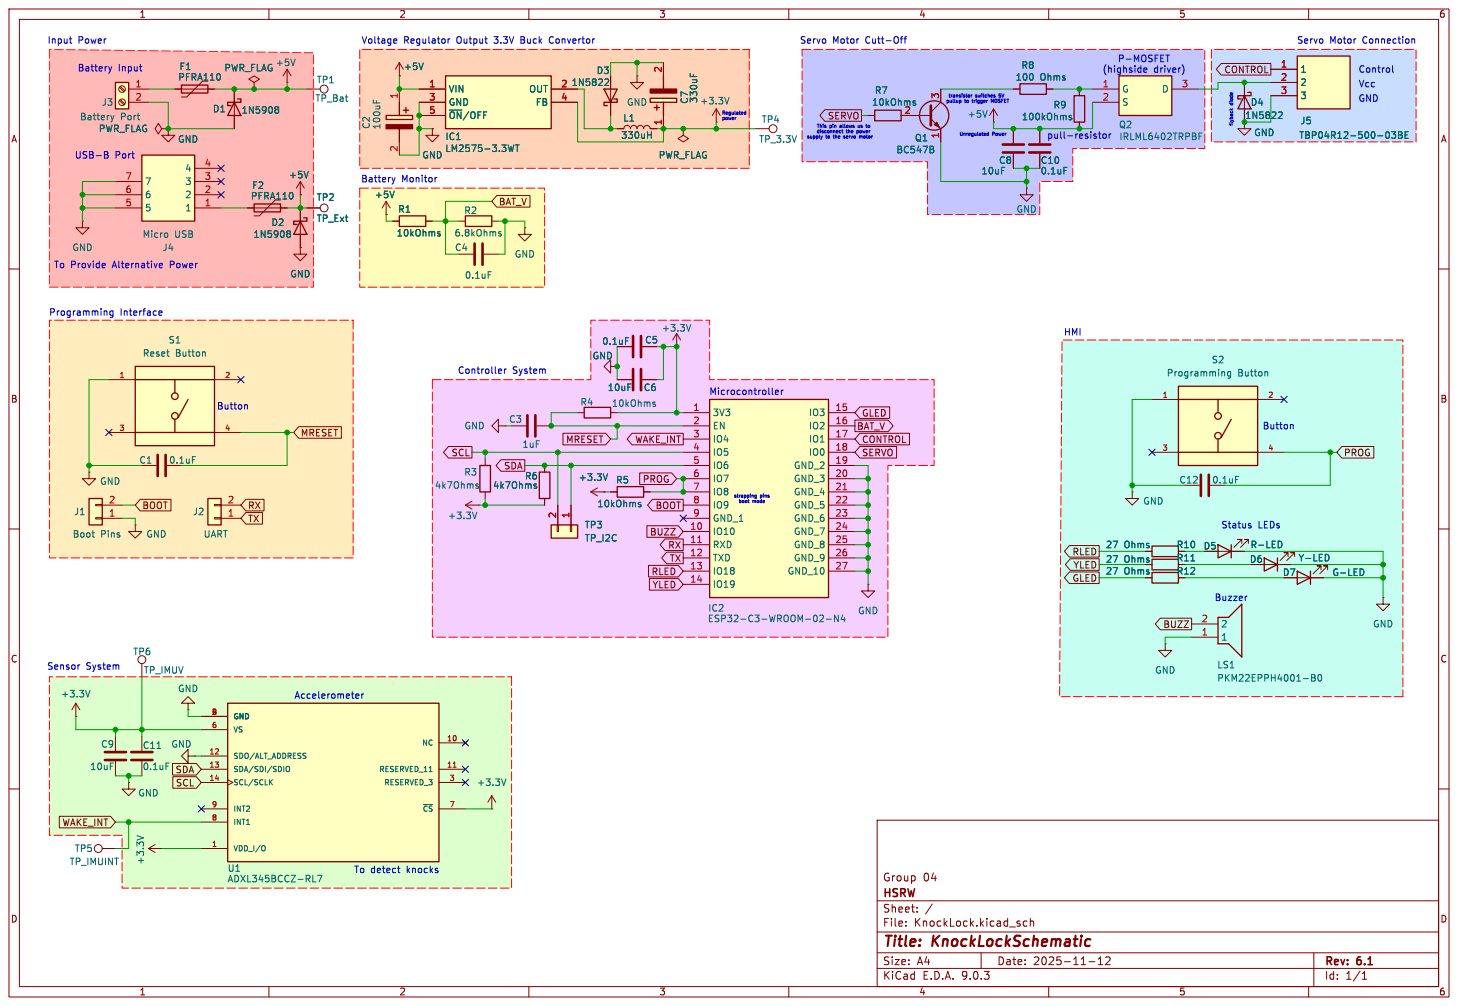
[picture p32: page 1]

Group 04
File: KnockLock.kicad_sch Sheet: / HSRW

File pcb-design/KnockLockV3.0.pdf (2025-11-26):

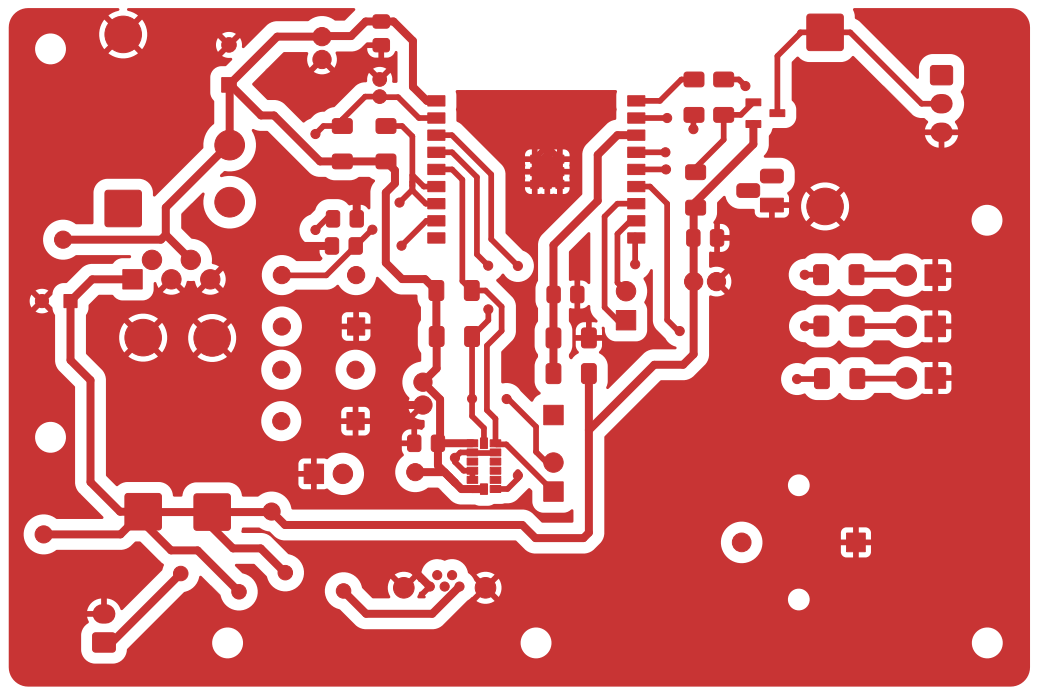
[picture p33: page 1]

Group 04
File: KnockLock.kicad_pcb Sheet: HSRW

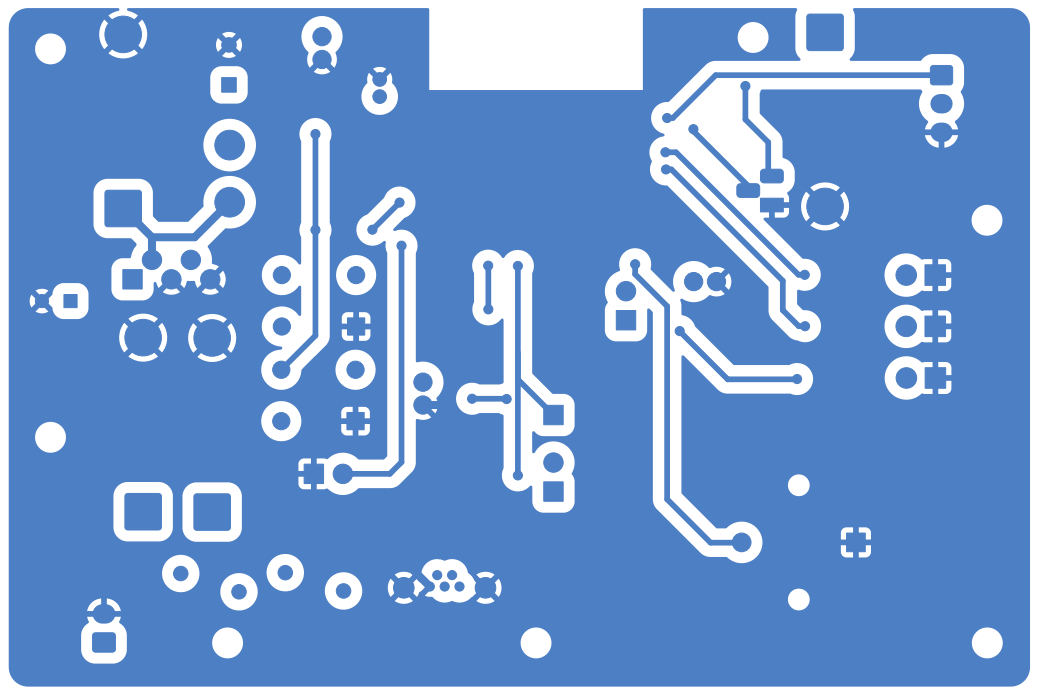
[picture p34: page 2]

Group 04
File: KnockLock.kicad_pcb Sheet: HSRW

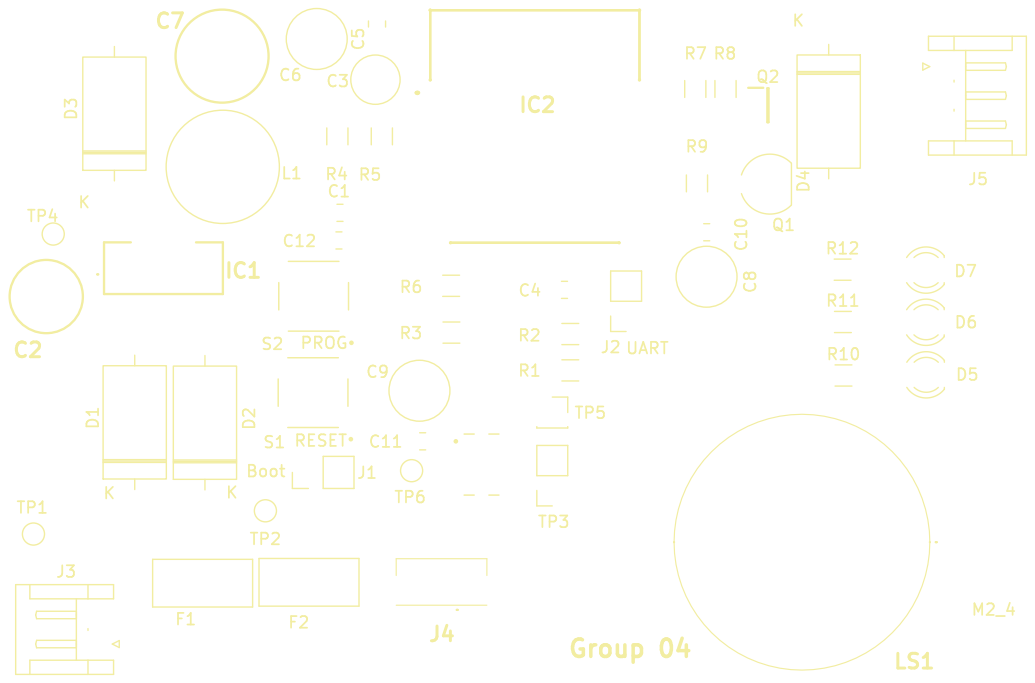
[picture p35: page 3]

Group 04
File: KnockLock.kicad_pcb Sheet: HSRW

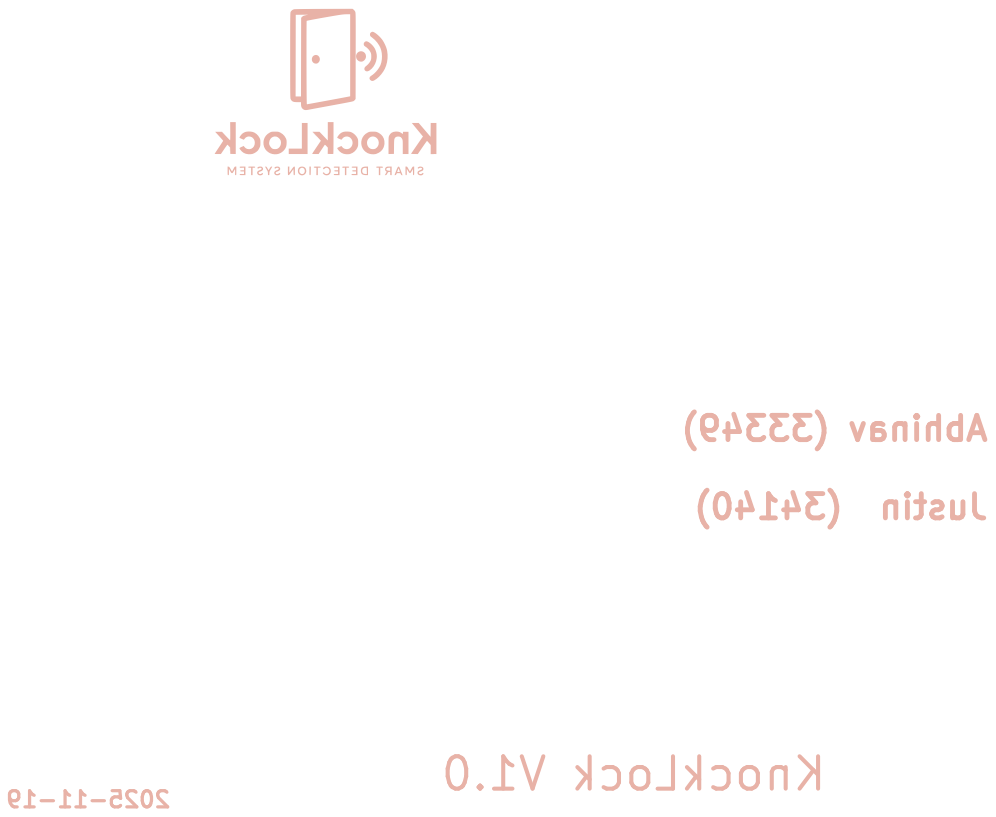
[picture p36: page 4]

Group 04
File: KnockLock.kicad_pcb Sheet: HSRW

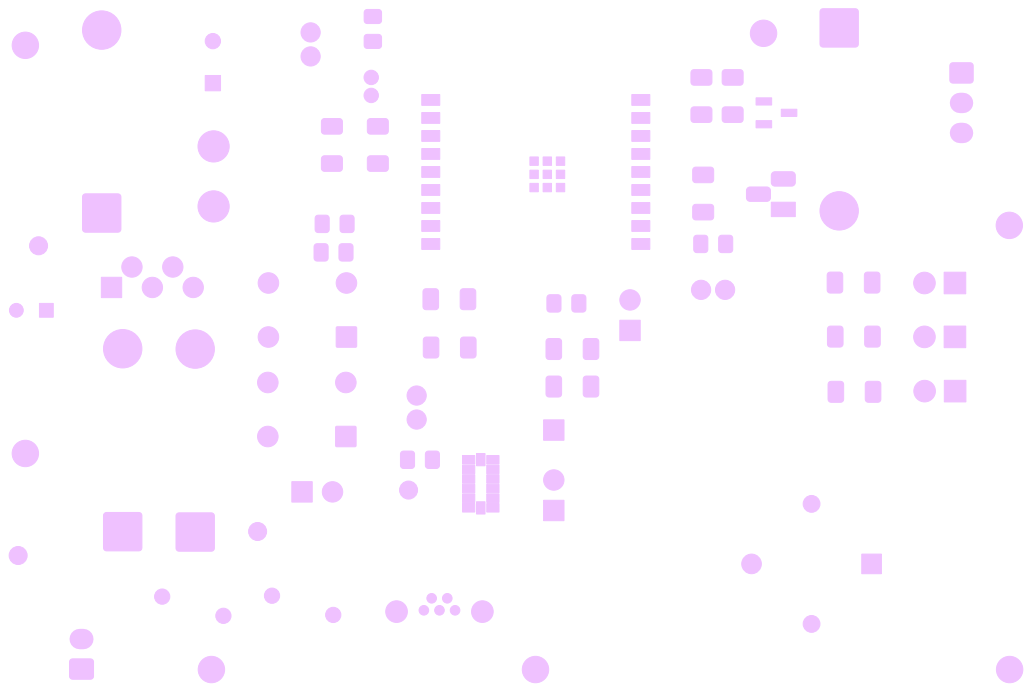
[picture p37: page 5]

Group 04
File: KnockLock.kicad_pcb Sheet: HSRW

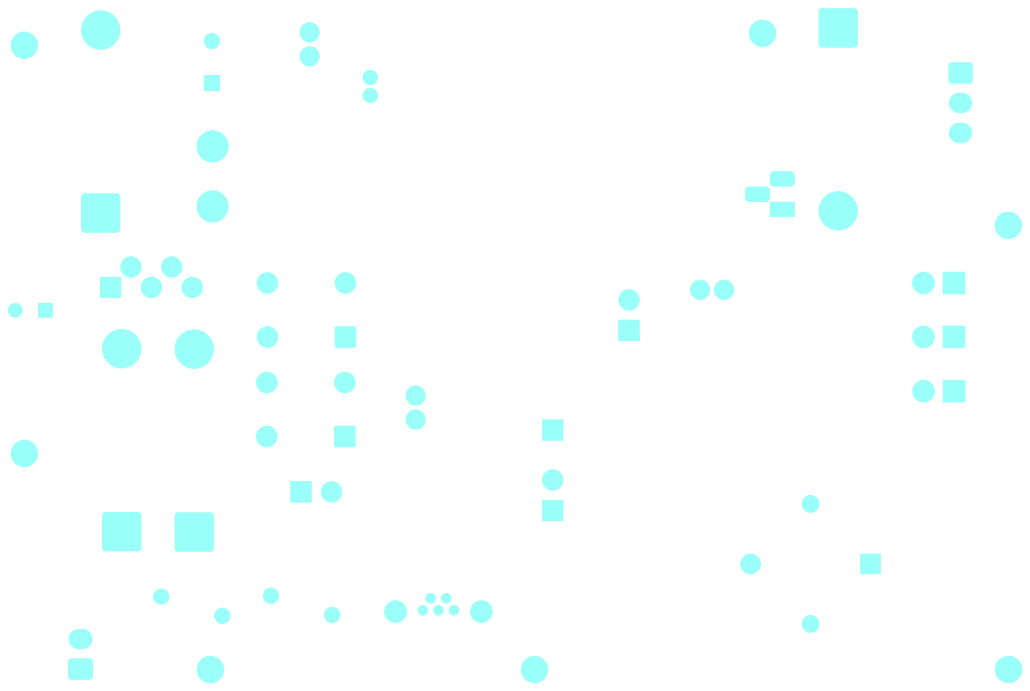
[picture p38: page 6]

Group 04
File: KnockLock.kicad_pcb Sheet: HSRW

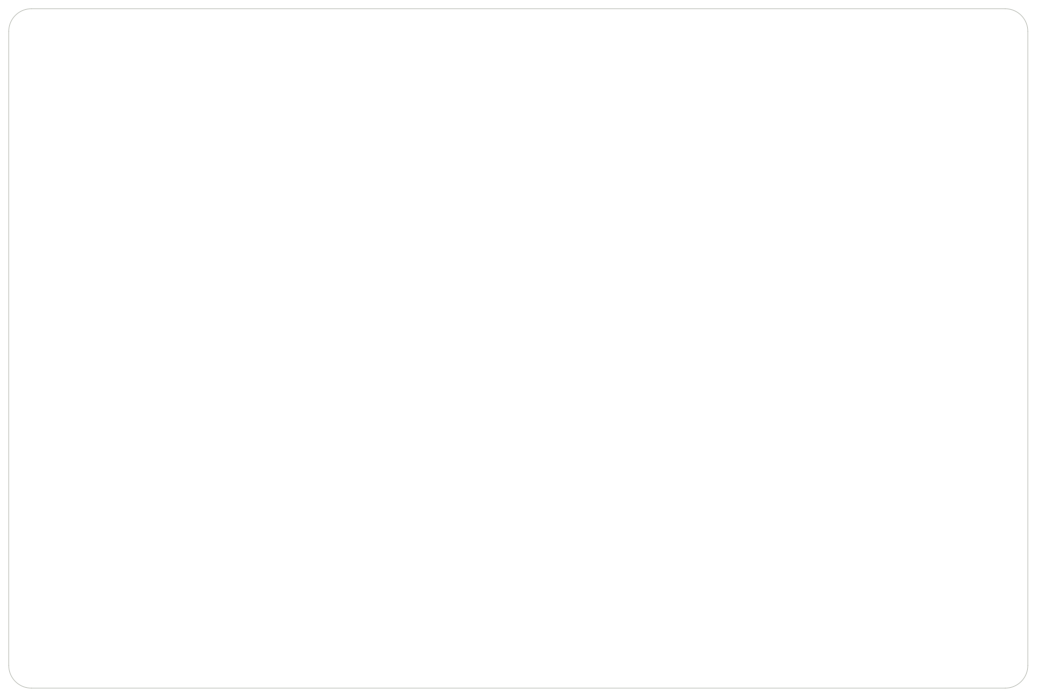
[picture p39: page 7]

Group 04
File: KnockLock.kicad_pcb Sheet: HSRW

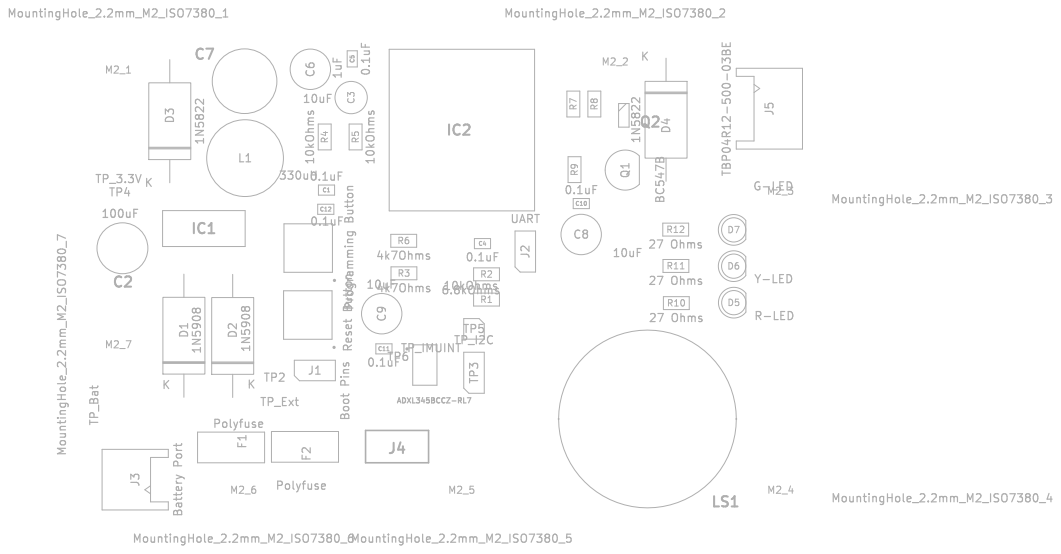
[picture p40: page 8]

Group 04
File: KnockLock.kicad_pcb Sheet: HSRW

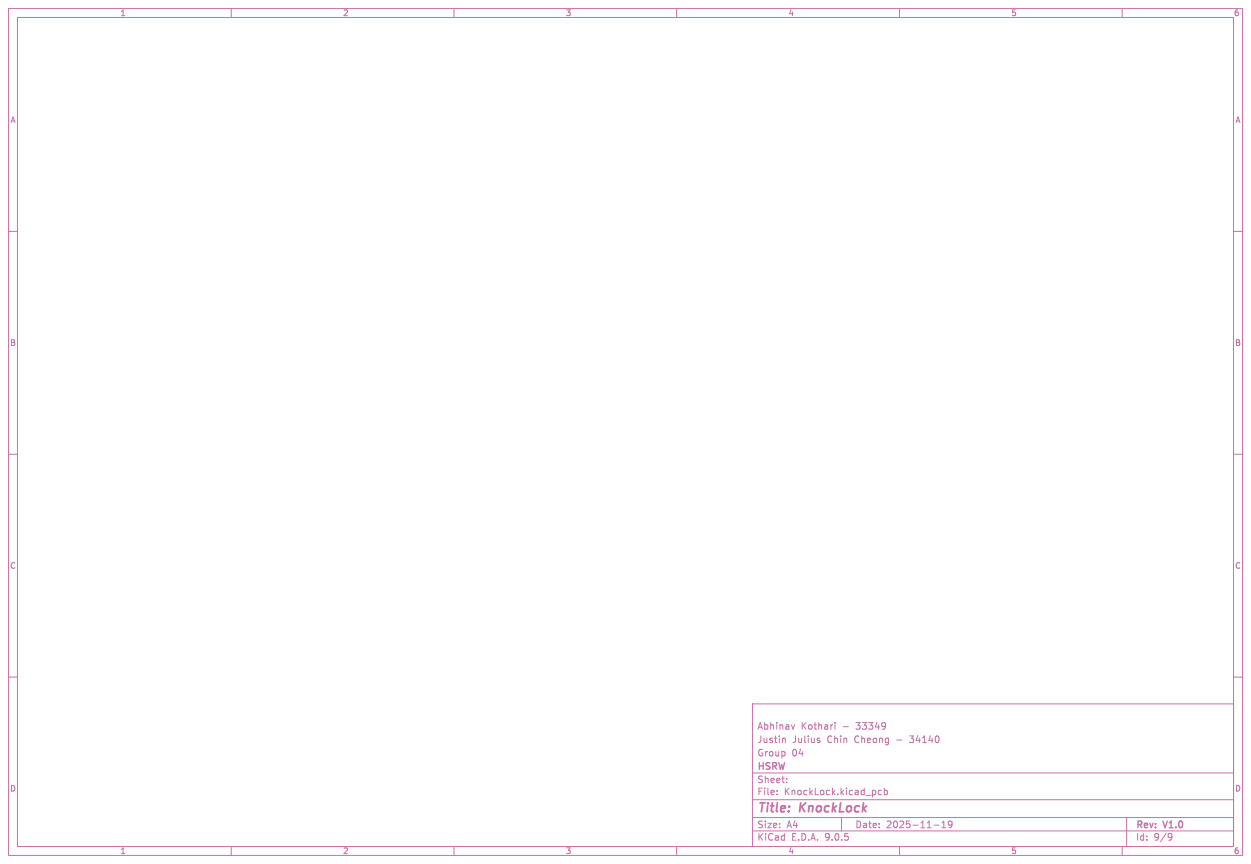
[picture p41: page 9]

Group 04
File: KnockLock.kicad_pcb Sheet: HSRW

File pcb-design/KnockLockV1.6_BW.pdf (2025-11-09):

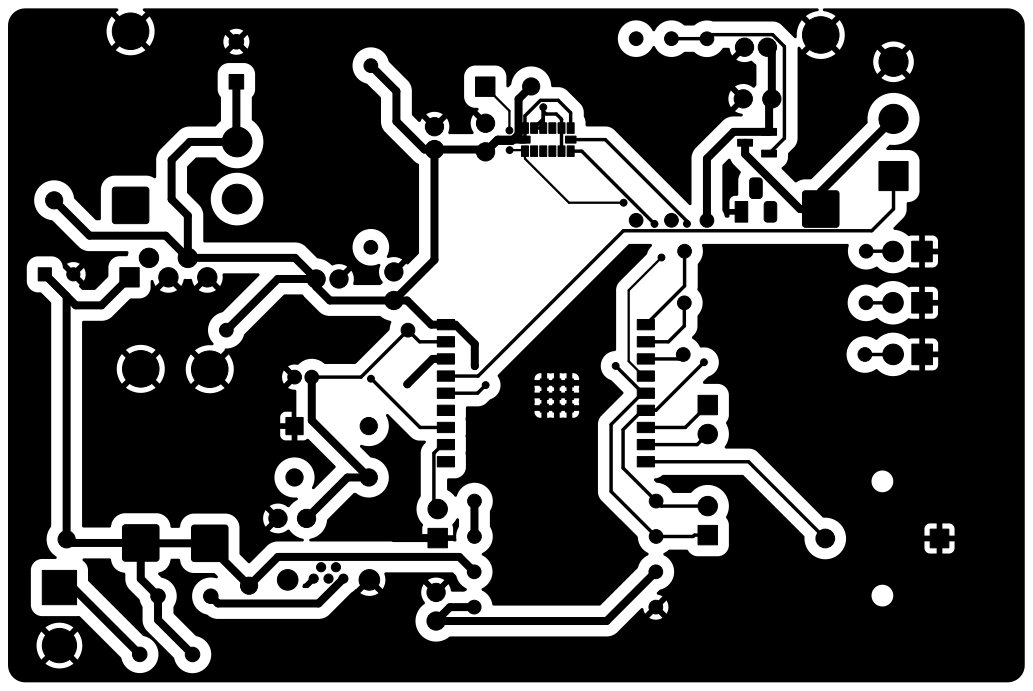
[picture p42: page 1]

Group 04
File: KnockLock.kicad_pcb Sheet: HSRW

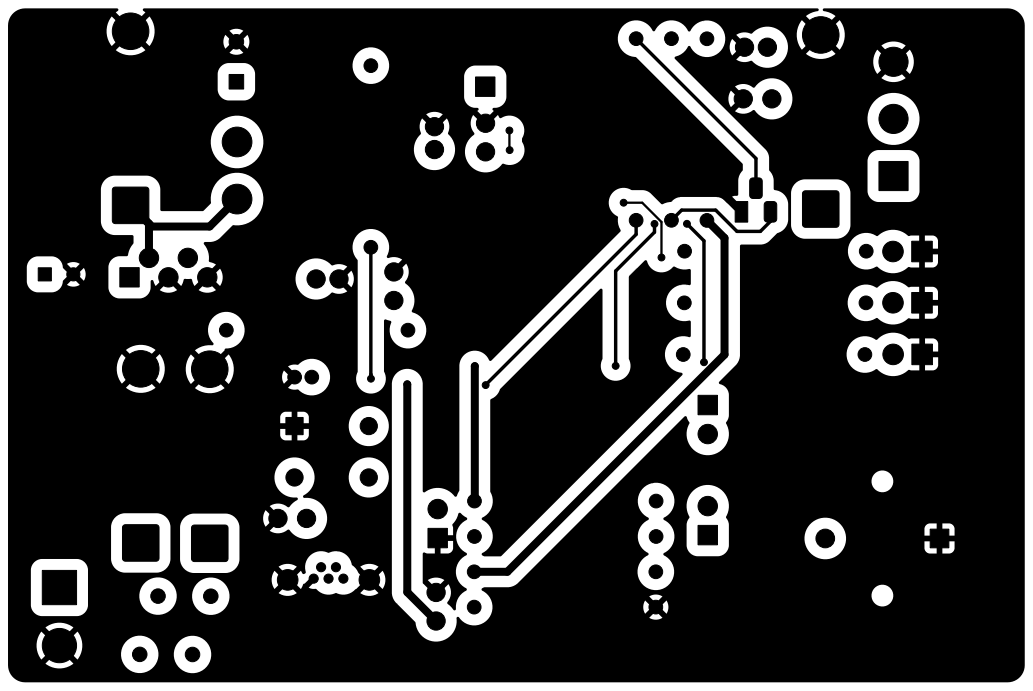
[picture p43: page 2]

Group 04
File: KnockLock.kicad_pcb Sheet: HSRW


Group 04
File: KnockLock.kicad_pcb Sheet: HSRW


Group 04
File: KnockLock.kicad_pcb Sheet: HSRW


Group 04
File: KnockLock.kicad_pcb Sheet: HSRW


Group 04
File: KnockLock.kicad_pcb Sheet: HSRW


Group 04
File: KnockLock.kicad_pcb Sheet: HSRW


Group 04
File: KnockLock.kicad_pcb Sheet: HSRW


Group 04
File: KnockLock.kicad_pcb Sheet: HSRW

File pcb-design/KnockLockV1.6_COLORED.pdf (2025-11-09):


Group 04
File: KnockLock.kicad_pcb Sheet: HSRW


Group 04
File: KnockLock.kicad_pcb Sheet: HSRW


Group 04
File: KnockLock.kicad_pcb Sheet: HSRW


Group 04
File: KnockLock.kicad_pcb Sheet: HSRW


Group 04
File: KnockLock.kicad_pcb Sheet: HSRW


Group 04
File: KnockLock.kicad_pcb Sheet: HSRW


Group 04
File: KnockLock.kicad_pcb Sheet: HSRW


Group 04
File: KnockLock.kicad_pcb Sheet: HSRW


Group 04
File: KnockLock.kicad_pcb Sheet: HSRW

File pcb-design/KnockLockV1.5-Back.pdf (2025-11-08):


Group 04
File: KnockLock.kicad_pcb Sheet: HSRW

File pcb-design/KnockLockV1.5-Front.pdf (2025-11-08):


Group 04
File: KnockLock.kicad_pcb Sheet: HSRW


Group 04
File: KnockLock.kicad_pcb Sheet: HSRW

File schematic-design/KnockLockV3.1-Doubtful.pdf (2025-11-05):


Group 04
File: KnockLock.kicad_sch Sheet: / HSRW

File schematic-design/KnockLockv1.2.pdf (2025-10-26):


Servo Motor Connection Control and Sensor System

there is some activity

Group 04
File: KnockLock.kicad_sch Sheet: / HSRW


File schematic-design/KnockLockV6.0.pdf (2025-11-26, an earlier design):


File: KnockLock.kicad_sch Sheet: / HSRW

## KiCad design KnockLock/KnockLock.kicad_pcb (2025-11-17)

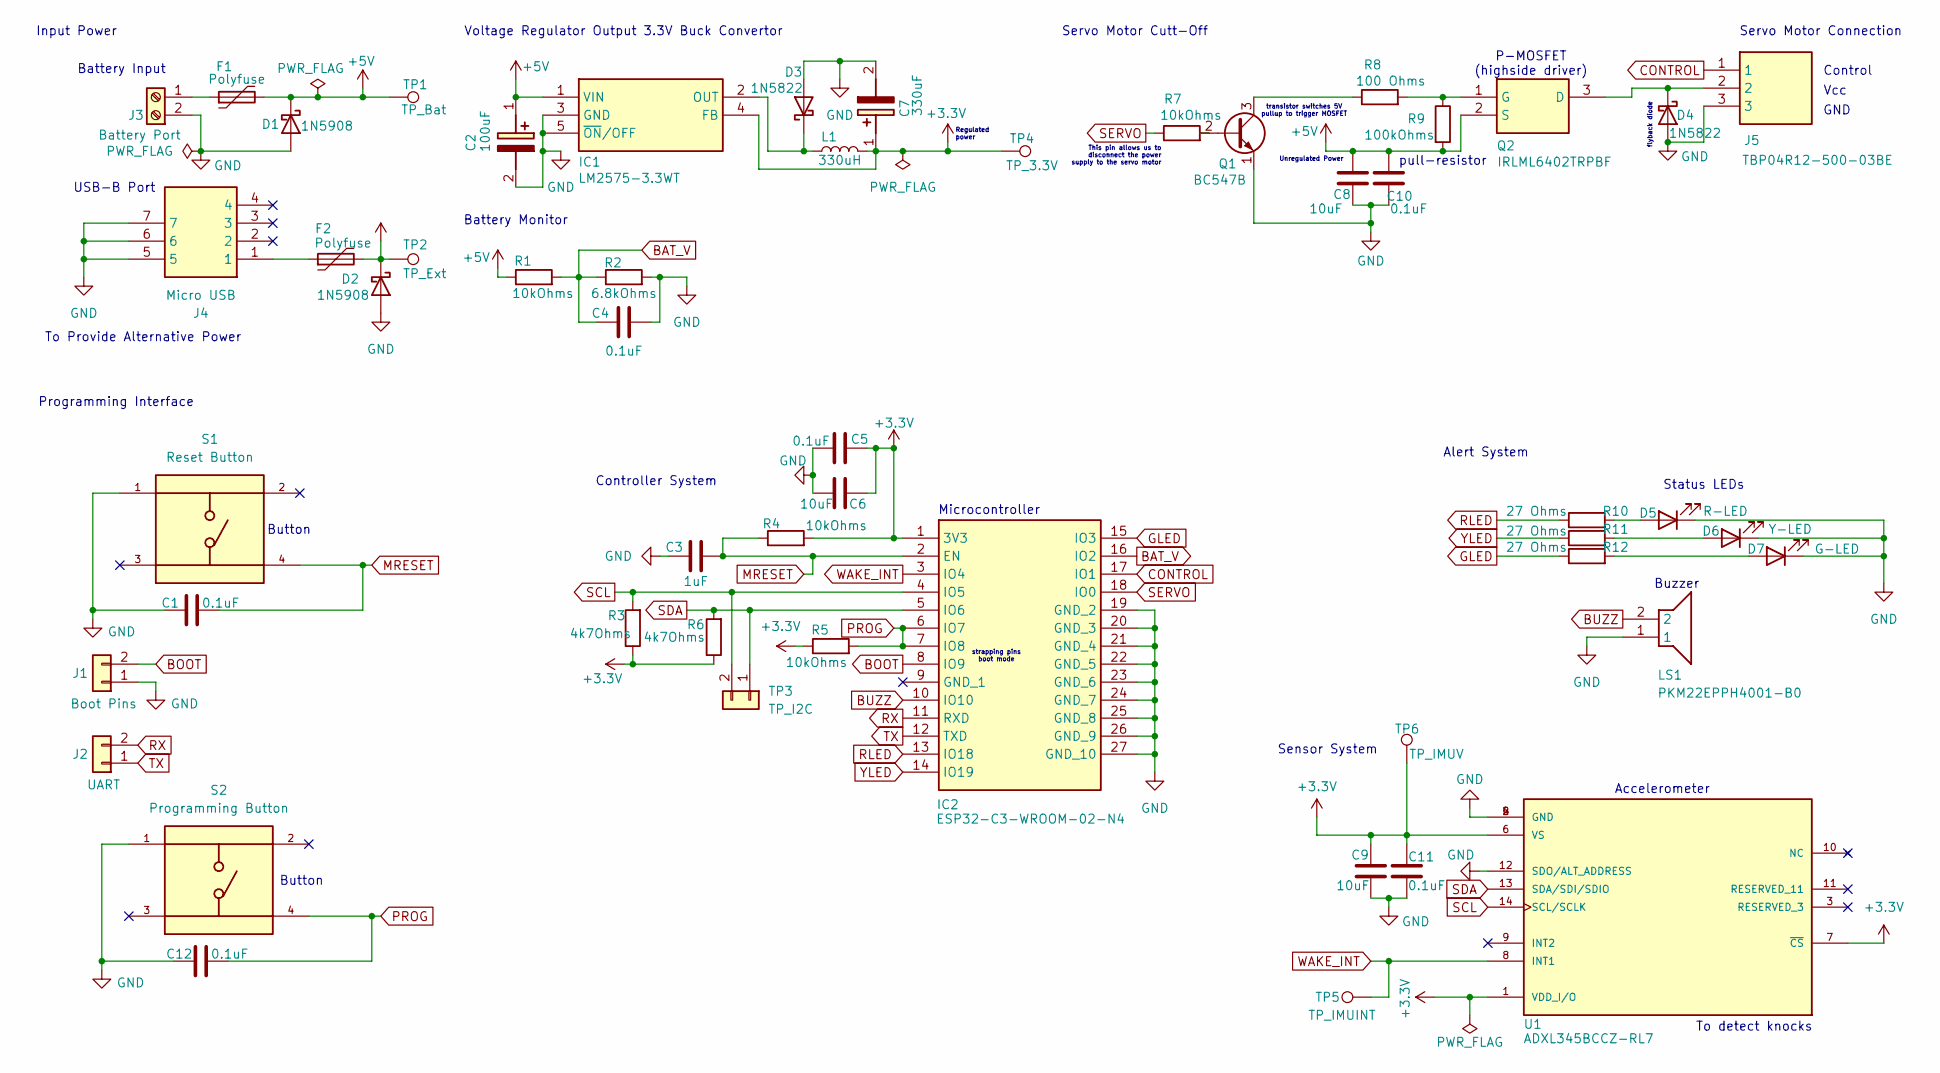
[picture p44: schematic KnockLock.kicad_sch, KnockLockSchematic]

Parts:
C1, C4, C5, C10, C11, C12: 0.1uF; C_0805_2012Metric_Pad1.18x1.45mm_HandSolder
C2: 100uF; CAPPRD250W55D630H1220; Mouser Part Number 667-EEU-FC1C101H
C3: 1uF; C_Radial_D4.0mm_H7.0mm_P1.50mm
C6, C8, C9: 10uF; C_Radial_D5.0mm_H11.0mm_P2.00mm
C7: 330uF; CAPPRD350W65D800H1300; Mouser Part Number 667-EEU-FR1E331
D1, D2: 1N5908; D_DO-201AD_P15.24mm_Horizontal
D3, D4: 1N5822; D_DO-201AD_P15.24mm_Horizontal
D5: R-LED; LED_D3.0mm
D6: Y-LED; LED_D3.0mm
D7: G-LED; LED_D3.0mm
F1, F2: Polyfuse; Fuse_BelFuse_0ZRE0012FF_L8.3mm_W3.8mm
IC1: LM2575-3.3WT; LM257533WT; Mouser Part Number 998-LM2575-3.3WT
IC2: ESP32-C3-WROOM-02-N4; ESP32C3WROOM02N4; Mouser Part Number 356-ESP32C3WROOM02N4
J1: Boot Pins; PinHeader_1x02_P2.54mm_Vertical
J2: UART; PinSocket_1x02_P2.54mm_Vertical
J3: Battery Port; TerminalBlock_bornier-2_P5.08mm
J4: Micro USB; USB3145301A; Mouser Part Number 640-USB3145-30-1-A
J5: TBP04R12-500-03BE; JST_EH_S3B-EH_1x03_P2.50mm_Horizontal; Mouser Part Number 179-TBP04R12-50003BE
L1: 330uH; L_Radial_D9.5mm_P5.00mm_Fastron_07HVP
LS1: PKM22EPPH4001-B0; PKM22EPPH4001B0; Mouser Part Number 81-PKM22EPPH4001-B0
Q1: BC547B; TO-92_HandSolder
Q2: IRLML6402TRPBF; SOT95P237X112-3N; Mouser Part Number 942-IRLML6402TRPBF
R1, R4, R5, R7: 10kOhms; R_1206_3216Metric_Pad1.30x1.75mm_HandSolder
R2: 6.8kOhms; R_1206_3216Metric_Pad1.30x1.75mm_HandSolder
R3, R6: 4k7Ohms; R_1206_3216Metric_Pad1.30x1.75mm_HandSolder
R8: 100 Ohms; R_1206_3216Metric_Pad1.30x1.75mm_HandSolder
R9: 100kOhms; R_1206_3216Metric_Pad1.30x1.75mm_HandSolder
R10, R11, R12: 27 Ohms; R_1206_3216Metric_Pad1.30x1.75mm_HandSolder
S1: Reset Button; SW_TS02-66-60-BK-260-LCR-D; PARTREV 1.0
S2: Programming Button; SW_TS02-66-60-BK-260-LCR-D; PARTREV 1.0
TP1: TP_Bat; TestPoint_Pad_D1.5mm
TP2: TP_Ext; TestPoint_Pad_D1.5mm
TP3: TP_I2C; PinSocket_1x02_P2.54mm_Vertical
TP4: TP_3.3V; TestPoint_Pad_D1.5mm
TP5: TP_IMUINT; PinSocket_1x01_P2.54mm_Vertical
TP6: TP_IMUV; TestPoint_Pad_D1.5mm
U1: ADXL345BCCZ-RL7; PQFN80P500X300X100-14N; PARTREV B

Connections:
+3.3V: C5.2, C6.2, C7.1 (+), C9.2, C11.2, IC1.4 (FB), IC2.1 (3V3), L1.2, R3.1, R4.2, R5.1, R6.1, TP4.1, TP6.1, U1.1 (VDD_I/O), U1.6 (VS), U1.7 (~CS)
+5V: C2.1 (+), C8.2, C10.2, D1.1 (K), D2.1 (K), F1.2, F2.2, IC1.1 (VIN), Q2.2 (S), R1.1, R9.2, TP1.1, TP2.1
BAT_V: C4.1, IC2.16 (IO2), R1.2, R2.1
BOOT: IC2.8 (IO9), J1.2
BUZZ: IC2.10 (IO10), LS1.2
CONTROL: IC2.17 (IO1), J5.1
GLED: IC2.15 (IO3), R12.1
GND: C1.1, C2.2 (-), C3.2, C4.2, C5.1, C6.1, C7.2 (-), C8.1, C9.1, C10.1, C11.1, C12.1, D1.2 (A), D2.2 (A), D3.2 (A), D4.2 (A), D5.1 (K), D6.1 (K), D7.1 (K), IC1.3 (GND), IC1.5 (~ON/OFF), IC2.19 (GND_2), IC2.20 (GND_3), IC2.21 (GND_4), IC2.22 (GND_5), IC2.23 (GND_6), IC2.24 (GND_7), IC2.25 (GND_8), IC2.26 (GND_9), IC2.27 (GND_10), J1.1, J3.2, J4.5, J4.6, J4.7, J5.3, LS1.1, Q1.1 (E), R2.2, S1.1, S2.1, U1.2 (GND), U1.4 (GND), U1.5 (GND), U1.12 (SDO/ALT_ADDRESS)
MRESET: C1.2, C3.1, IC2.2 (EN), R4.1, S1.4
unnamed: D3.1 (K), IC1.2 (OUT), L1.1
unnamed: D4.1 (K), J5.2, Q2.3 (D)
unnamed: D5.2 (A), R10.2
unnamed: D6.2 (A), R11.2
unnamed: D7.2 (A), R12.2
unnamed: F2.1, J4.1
unnamed: F1.1, J3.1
unnamed: Q1.2 (B), R7.2
unnamed: Q1.3 (C), R8.1
unnamed: Q2.1 (G), R8.2, R9.1
PROG: C12.2, IC2.6 (IO7), IC2.7 (IO8), R5.2, S2.4
RLED: IC2.13 (IO18), R10.1
RX: IC2.11 (RXD), J2.2
SCL: IC2.4 (IO5), R3.2, TP3.2, U1.14 (SCL/SCLK)
SDA: IC2.5 (IO6), R6.2, TP3.1, U1.13 (SDA/SDI/SDIO)
SERVO: IC2.18 (IO0), R7.1
TX: IC2.12 (TXD), J2.1
WAKE_INT: IC2.3 (IO4), TP5.1, U1.8 (INT1)
YLED: IC2.14 (IO19), R11.1

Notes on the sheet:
Voltage Regulator Output 3.3V Buck Convertor
Vcc
Battery Input
P-MOSFET (highside driver)
Controller System
To detect knocks
Control
Button
Programming Interface
flyback diode
strapping pins boot mode
Unregulated Power
Servo Motor Cutt-Off
Regulated power
Sensor System
GND
Buzzer
transistor switches 5V pullup to trigger MOSFET
Alert System
Servo Motor Connection
This pin allows us to disconnect the power supply to the servo motor
Input Power
Microcontroller
Accelerometer
Battery Monitor
Status LEDs
To Provide Alternative Power
USB-B Port
pull-resistor

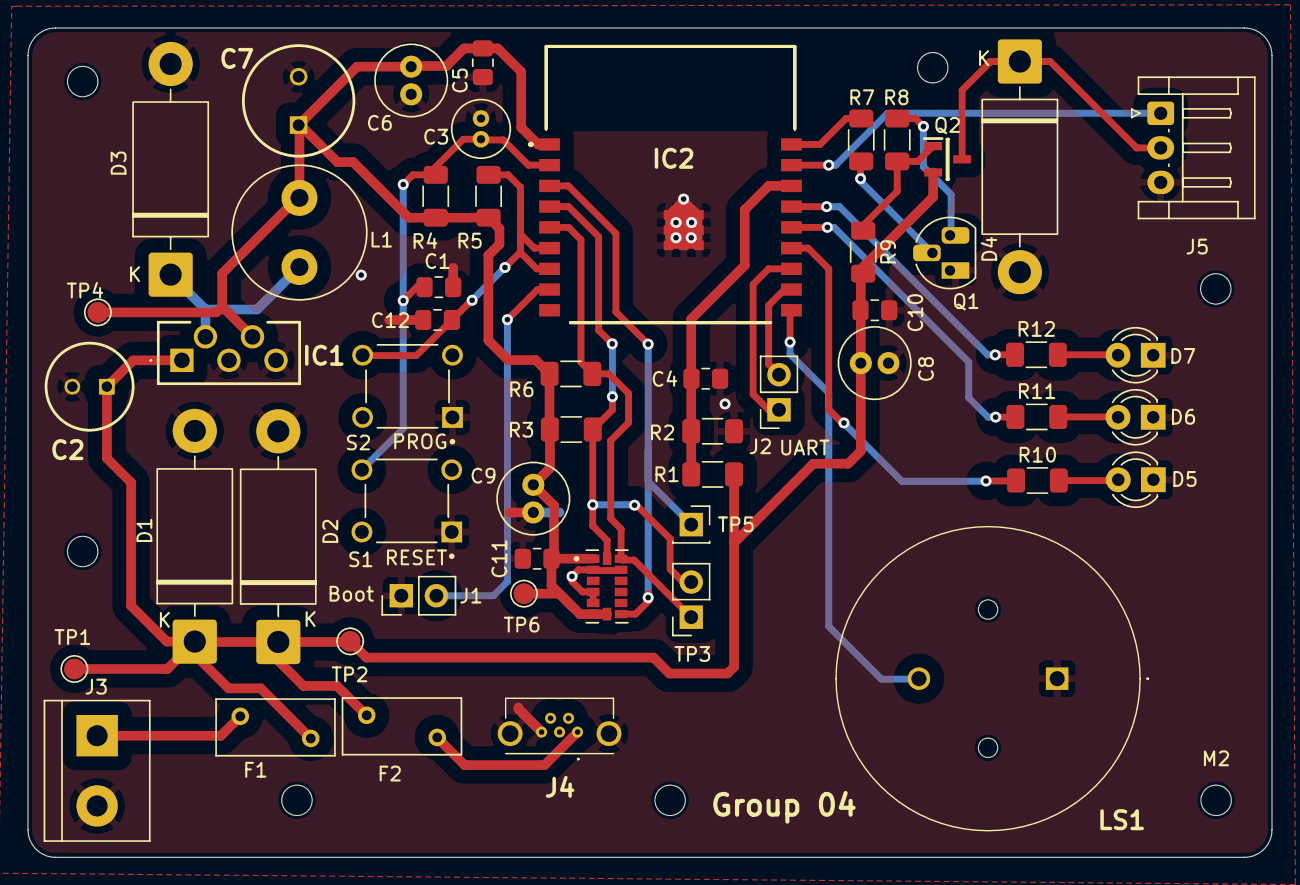
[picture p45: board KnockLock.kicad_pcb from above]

Board: 2 copper layers, 90.0 x 60.0 mm, 55 parts (0 on the bottom side), 28 nets.

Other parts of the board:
M2, M2#2: MountingHole_2.2mm_M2_ISO7380

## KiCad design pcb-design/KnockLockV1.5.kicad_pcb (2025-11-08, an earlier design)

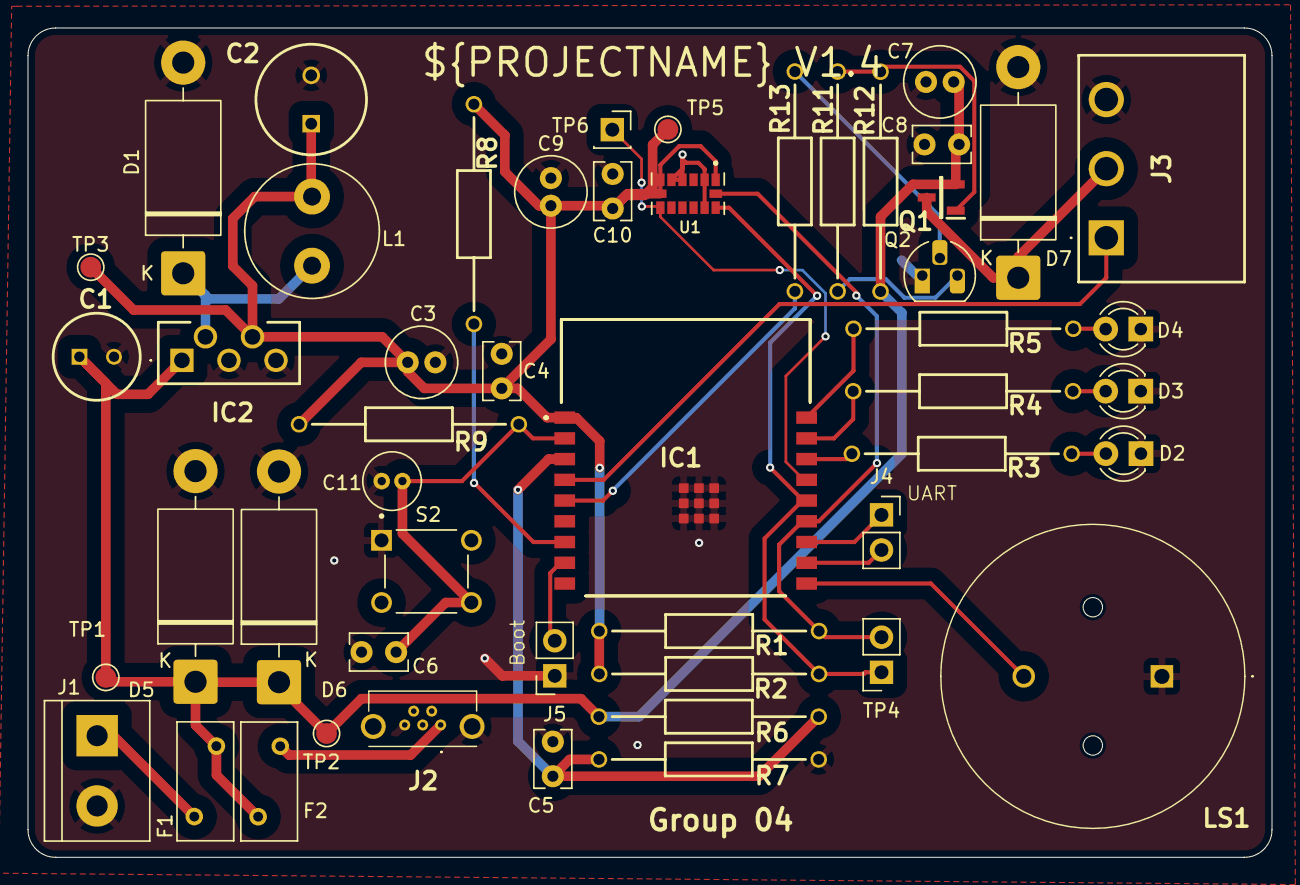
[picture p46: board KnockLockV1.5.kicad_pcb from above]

Board: 2 copper layers, 90.0 x 60.0 mm, 51 parts (0 on the bottom side), 28 nets.

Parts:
C1: 100uF; CAPPRD250W55D630H1220
C2: 330uF; CAPPRD350W65D800H1300
C3, C7, C9: 10uF; C_Radial_D5.0mm_H11.0mm_P2.00mm
C4, C5, C6, C8, C10: 0.1uF; C_Rect_L4.0mm_W2.5mm_P2.50mm
C11: 1uF; C_Radial_D4.0mm_H7.0mm_P1.50mm
D1, D5, D6, D7: 1N5822; D_DO-201AD_P15.24mm_Horizontal
D2: R-LED; LED_D3.0mm
D3: Y-LED; LED_D3.0mm
D4: G-LED; LED_D3.0mm
F1, F2: Polyfuse; Fuse_BelFuse_0ZRE0012FF_L8.3mm_W3.8mm
IC1: ESP32-C3-WROOM-02-N4; ESP32C3WROOM02N4
IC2: LM2575-3.3WT; LM257533WT
J1: Screw_Terminal_01x02; TerminalBlock_bornier-2_P5.08mm
J2: USB3145-30-1-A; USB3145301A
J3: TBP04R12-500-03BE; TBP04R1250003BE
J4: UART; PinSocket_1x02_P2.54mm_Vertical
J5: Boot Pins; PinSocket_1x02_P2.54mm_Vertical
L1: 330uH; L_Radial_D9.5mm_P5.00mm_Fastron_07HVP
LS1: PKM22EPPH4001-B0; PKM22EPPH4001B0
Q1: IRLML6402TRPBF; SOT95P237X112-3N
Q2: BC547B; TO-92_HandSolder
R1, R2: 4k7Ohms; RESAD1590W60L630D240
R3, R4, R5: 27 Ohms; RESAD1590W60L630D240
R6, R8, R9, R13: 10kOhms; RESAD1590W60L630D240
R7: 6.8kOhms; RESAD1590W60L630D240
R11: 100 Ohms; RESAD1590W60L630D240
R12: 100kOhms; RESAD1590W60L630D240
S2: TS02-66-60-BK-260-LCR-D; SW_TS02-66-60-BK-260-LCR-D
TP1: TP_Bat; TestPoint_Pad_D1.5mm
TP2: TP_Ext; TestPoint_Pad_D1.5mm
TP3: TP_3.3V; TestPoint_Pad_D1.5mm
TP4: TP_I2C; PinSocket_1x02_P2.54mm_Vertical
TP5: TP_IMUV; TestPoint_Pad_D1.5mm
TP6: TP_IMUINT; PinSocket_1x01_P2.54mm_Vertical
U1: ADXL345BCCZ-RL7; PQFN80P500X300X100-14N

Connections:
+3.3V: C2.1 (+), C3.2, C4.2, C9.2, C10.2, IC1.1 (3V3), IC2.4 (FB), L1.2, R1.1, R2.1, R8.1, R9.2, TP3.1, TP5.1, U1.1 (VDD_I/O), U1.6 (VS), U1.7 (~CS)
+5V: C1.1 (+), C7.2, C8.2, D5.1 (K), D6.1 (K), F1.2, F2.2, IC2.1 (VIN), Q1.2 (S), R6.1, R12.2, TP1.1, TP2.1
BAT_V: C5.1, IC1.3 (IO4), R6.2, R7.1
BOOT: IC1.8 (IO9), J5.2
BUZZ: IC1.10 (IO10), LS1.2
CONTROL: IC1.4 (IO5), J3.1
GLED: IC1.18 (IO0), R5.1
GND: C1.2 (-), C2.2 (-), C3.1, C4.1, C5.2, C6.1, C7.1, C8.1, C9.1, C10.1, C11.2, D1.2 (A), D2.1 (K), D3.1 (K), D4.1 (K), D5.2 (A), D6.2 (A), D7.2 (A), IC1.19 (GND_2), IC1.20 (GND_3), IC1.21 (GND_4), IC1.22 (GND_5), IC1.23 (GND_6), IC1.24 (GND_7), IC1.25 (GND_8), IC1.26 (GND_9), IC1.27 (GND_10), IC2.3 (GND), IC2.5 (~ON/OFF), J1.2, J2.5, J2.6, J2.7, J3.3, J5.1, LS1.1, Q2.1 (E), R7.2, S2.1, U1.2 (GND), U1.4 (GND), U1.5 (GND), U1.12 (SDO/ALT_ADDRESS)
MRESET: C6.2, C11.1, IC1.2 (EN), R9.1, S2.4
unnamed: D1.1 (K), IC2.2 (OUT), L1.1
unnamed: D2.2 (A), R3.2
unnamed: D3.2 (A), R4.2
unnamed: D4.2 (A), R5.2
unnamed: D7.1 (K), J3.2, Q1.3 (D)
unnamed: F2.1, J2.1
unnamed: IC1.7 (IO8), R8.2
unnamed: F1.1, J1.1
unnamed: Q1.1 (G), R11.2, R12.1
unnamed: Q2.2 (B), R13.2
unnamed: Q2.3 (C), R11.1
RLED: IC1.16 (IO2), R3.1
RX: IC1.11 (RXD), J4.2
SCL: IC1.13 (IO18), R1.2, TP4.2, U1.14 (SCL/SCLK)
SDA: IC1.14 (IO19), R2.2, TP4.1, U1.13 (SDA/SDI/SDIO)
SERVO: IC1.5 (IO6), R13.1
TX: IC1.12 (TXD), J4.1
WAKE_INT: IC1.15 (IO3), TP6.1, U1.8 (INT1)
YLED: IC1.17 (IO1), R4.1

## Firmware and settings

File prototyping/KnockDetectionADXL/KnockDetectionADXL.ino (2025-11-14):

#include <ESP32Servo.h>

#include <Wire.h>
#include <SparkFun_ADXL345.h>  // SparkFun ADXL345 Library


/*
  Authors: Justin Julius Chin Cheong 34140, Abhinav Kothari 33349
  Project: Knock Pattern Detection using ESP32 + ADXL345
  Description:
    Detects specific knock patterns based on acceleration spikes.
    If no knock is detected for 5 seconds after the last one, resets detection.
*/

// --- Servo ----
Servo lockServo;

// ---- Sensor ----
ADXL345 adxl = ADXL345();  // Use for I2C communication

// ---- Pin Definitions ----
const int SDA_PIN = 4;
const int SCL_PIN = 5;
const int SERVO_PIN = 6;
const int BUZZER  = 10;
const int RLED = 3;
const int YLED = 18;
const int GLED = 19;

// ---- Knock Detection Parameters ----
const float KNOCK_THRESHOLD = 0.4;     // g-force above 1g baseline to count as a knock
const int PATTERN_TIMEOUT   = 3000;    // ms: time to check pattern after last knock
const int MAX_KNOCKS = 10;
const int KNOCK_TOL = 100;             // ms tolerance for pattern matching

// ---- Knock Pattern Variables ----
unsigned long knockTimes[MAX_KNOCKS];
int knockCount = 0;
unsigned long lastKnockTime = 0;

// ---- Pattern Definition ----
int targetPattern[] = {460, 430, 260, 190, 440, 430};
int patternLength = sizeof(targetPattern) / sizeof(targetPattern[0]);

// ---------------------------------------------------
void setup() {
  Serial.begin(9600);
  Serial.println("Initializing ADXL345...");
  Wire.begin(SDA_PIN, SCL_PIN);

  adxl.powerOn();
  adxl.setRangeSetting(2 ); // ±2g for better sensitivity

  pinMode(BUZZER, OUTPUT);
  pinMode(RLED, OUTPUT);
  pinMode(YLED, OUTPUT);
  pinMode(GLED, OUTPUT);

  digitalWrite(YLED, HIGH);

  Serial.println("Knock Detection Ready!");

  // Servo Setup
  ESP32PWM::allocateTimer(0);
  lockServo.setPeriodHertz(50); // standard 50 Hz servo
  lockServo.attach(SERVO_PIN, 500, 2500); // min/max pulse width for most servos
  lockServo.write(0); // locked position
}

// ---------------------------------------------------
void loop() {
  int x, y, z;
  adxl.readAccel(&x, &y, &z);

  // Convert to g-units (each LSB = 3.9 mg in ±2g mode)
  float xg = x * 0.0039;
  float yg = y * 0.0039;
  float zg = z * 0.0039;

  // Compute total acceleration magnitude
  float aMag = sqrt(xg * xg + yg * yg + zg * zg);
  float aDynamic = abs(aMag - 1.0); // subtract gravity

  unsigned long now = millis();

  // ---- Knock Detection ----
  if (aDynamic > KNOCK_THRESHOLD) {
    if (now - lastKnockTime > 100) { // debounce
      knockTimes[knockCount++] = now;
      lastKnockTime = now;
      Serial.print("Knock #");
      Serial.println(knockCount);

      if (knockCount == 1)
        Serial.println("First knock detected!");

      // When enough knocks are recorded, check pattern
      if (knockCount >= 10) {
        checkPattern();
        resetPattern();
      }
    }
  }

  // ---- 3s pattern timeout ----
  if ((now - lastKnockTime > PATTERN_TIMEOUT) && knockCount > 1) {
    checkPattern();
    resetPattern();
  }

  delay(10);
}

// ---------------------------------------------------
void checkPattern() {
  if (knockCount < 2) return;

  int intervals[MAX_KNOCKS];
  for (int i = 1; i < knockCount; i++) {
    intervals[i - 1] = knockTimes[i] - knockTimes[i - 1];
    Serial.print("Knock Interval: ");
    Serial.println(intervals[i - 1]);
  }

  bool match = false;
  int diff;

  // ---- Sliding window pattern check ----
  if (knockCount - 1 >= patternLength) {
    for (int offset = 0; offset <= knockCount - 1 - patternLength; offset++) {
      bool segmentMatch = true;

      for (int j = 0; j < patternLength; j++) {
        diff = abs(intervals[offset + j] - targetPattern[j]);
        Serial.print("Interval diff (offset ");
        Serial.print(offset);
        Serial.print(", step ");
        Serial.print(j);
        Serial.print("): ");
        Serial.println(diff);

        if (diff > KNOCK_TOL) {
          segmentMatch = false;
          break;
        }
      }

      if (segmentMatch) {
        match = true;
        break;
      }
    }
  }

  if (match) {
    Serial.println("✅ Correct knock pattern detected!");
    goodBeep();
    unlockBox();
  } else {
    Serial.println("❌ Wrong pattern");
    badBeep();
  }
}

// ---------------------------------------------------
void unlockBox() {
  Serial.println("🔓 Unlocking...");
  lockServo.write(180); // Move servo to unlock position
  delay(4000);
  Serial.println("🔒 Locking again...");
  lockServo.write(0); // Back to locked position
}

// ---------------------------------------------------
void resetPattern() {
  digitalWrite(YLED, HIGH);
  digitalWrite(GLED, LOW);
  digitalWrite(RLED, LOW);
  knockCount = 0;
  lastKnockTime = 0;
  Serial.println("Pattern reset.");
}

// ---------------------------------------------------
// Success beep (pleasant)
void goodBeep() {
  digitalWrite(YLED, LOW);
  digitalWrite(GLED, HIGH);
  tone(BUZZER, 1000, 150);
  delay(150);
  tone(BUZZER, 1500, 200);
  delay(200);
  noTone(BUZZER);
}

// ---------------------------------------------------
// Error beep (less pleasant)
void badBeep() {
  digitalWrite(YLED, LOW);
  digitalWrite(RLED, HIGH);
  tone(BUZZER, 400, 200);
  delay(200);
  tone(BUZZER, 300, 250);
  delay(250);
  noTone(BUZZER);
}

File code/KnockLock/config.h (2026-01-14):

#ifndef CONFIG_H
#define CONFIG_H

// -------------------------------------------------------------
// KNOCK DETECTION SETTINGS
// -------------------------------------------------------------
constexpr int KNOCK_THRESHOLD     = 150;      // In raw ADXL values
constexpr int MAX_KNOCKS          = 30;       // Max length of pattern possible
constexpr int MIN_KNOCKS          = 5;        // Min length of pattern possible
constexpr int KNOCKS_TO_LOCK      = 2;        // Knocks to do in unlocked state to lock the box back
constexpr int KNOCK_TOL           = 150;      // How many milliseconds close to target pattern for correct recognition (Higher makes it easier to repeat knock but also less safe)
constexpr int DEBOUNCE_TIME       = 150;      // Minimum duration before next knock is detected
constexpr int PATTERN_TIMEOUT     = 2000;     // Max duration between two knocks
//constexpr int IDLE_RESET_TIME     = 5000;     // Max duration before going back to start of pattern recognition
constexpr int SLEEP_TIMEOUT       = 60000;    // 1 Minute

constexpr int ALLOWED_MISTAKES = 1;           // How many accidental knocks before or after can be tolerated

// -------------------------------------------------------------
// ADXL345 SETTINGS
// -------------------------------------------------------------
constexpr int SENSITIVITY         = 2;    // Sensitivity can be: +-2g, +-4g, +-8g, +-16g
constexpr int TAP_THRESHOLD       = 40;   // This is now g, it is 0-255 (62.5mg per increment)
constexpr int TAP_DURATION        = 20;   // In ms
constexpr int DOUBLE_TAP_LATENCY  = 80;   // In ms
constexpr int DOUBLE_TAP_WINDOW   = 200;  // In ms
constexpr int ADXL_EN_X           = 1;  // Turn individual sensing off (0) or on (1)
constexpr int ADXL_EN_Y           = 1;  // Turn individual sensing off (0) or on (1)
constexpr int ADXL_EN_Z           = 1;  // Turn individual sensing off (0) or on (1)

// -------------------------------------------------------------
// BATTERY SETTINGS
// -------------------------------------------------------------
constexpr float VOLTAGE_MULTIPLIER   = 2.47;  // To get correct voltage, may need to alter depending on resistors if changed
constexpr float LOW_BAT_THRESHOLD_V  = 4.6;   // 30% of 4xAA - low battery alert to starts below this voltage
constexpr unsigned long BAT_CHECK_INTERVAL = 900000; // in ms, interval to check battery (Set to 15 minutes by default)
constexpr int FLASHING_TIME = 60; // in seconds, to change how frequently the system wakes up to indicate low battery with Red LED

// -------------------------------------------------------------
// DEBUG SETTINGS
// -------------------------------------------------------------
constexpr int DEBUG_MODE = 0; // Make 1 to allow pattern setting in locked state or unlocked state
constexpr int SERIAL_MONITOR_EN   = 1;  // Turn Serial Monitor on with 1 and off with 0
// To enter manual override
constexpr int OVERRIDE_CLICK_COUNT = 4;     // Total clicks needed
constexpr int CLICK_GAP_TIMEOUT    = 500;   // Max time (ms) between clicks
#endif

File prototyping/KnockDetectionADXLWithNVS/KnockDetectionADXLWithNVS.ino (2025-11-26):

#include <ESP32Servo.h>
#include <Preferences.h>
#include <Wire.h>
#include <SparkFun_ADXL345.h>  // SparkFun ADXL345 Library

/*
  Authors: Justin Julius Chin Cheong 34140, Abhinav Kothari 33349
  Project: Knock Pattern Detection using ESP32 + ADXL345

  Features:
    • Detects knock patterns from acceleration spikes.
    • Saves & loads target pattern from ESP32 NVS.
    • Allows ±3 “junk knocks” before and after the correct pattern.
*/

// ---------------------- CONSTANTS ----------------------
const int SDA_PIN   = 4;
const int SCL_PIN   = 5;
const int SERVO_PIN = 6;
const int BUZZER    = 10;
const int RLED      = 18;
const int YLED      = 19;
const int GLED      = 3;

const float KNOCK_THRESHOLD = 0.4;  // g-force above baseline
const int PATTERN_TIMEOUT   = 3000;
const int MAX_KNOCKS        = 30;
const int KNOCK_TOL         = 150;  // ms tolerance

// Allow junk knocks
const int EXTRA_BEFORE = 3;   // allow 3 knocks before valid sequence
const int EXTRA_AFTER  = 3;   // allow 3 knocks after valid sequence

// ---------------------- VARIABLES ----------------------
Servo lockServo;
Preferences prefs;
ADXL345 adxl = ADXL345();

unsigned long knockTimes[MAX_KNOCKS];
int knockCount = 0;
unsigned long lastKnockTime = 0;

unsigned long targetPattern[MAX_KNOCKS];
int patternLength = 0;

// -------------------------------------------------------
// LOAD PATTERN FROM EEPROM
// -------------------------------------------------------
int loadPatternFromNVS(unsigned long intervals[]) {
  prefs.begin("knocks", true);  

  int count = prefs.getInt("count", -1);
  if (count <= 0) {
    prefs.end();
    Serial.println("⚠ No saved pattern found in NVS.");
    return -1;
  }

  for (int i = 0; i < count; i++) {
    char key[8];
    sprintf(key, "i%d", i);
    intervals[i] = prefs.getULong(key, 0);
  }

  prefs.end();
  Serial.printf("📥 Loaded %d knock intervals from NVS.\n", count);
  return count;
}

// -------------------------------------------------------
void setup() {
  Serial.begin(115200);
  Serial.println("\nInitializing ADXL345...");
  
  Wire.begin(SDA_PIN, SCL_PIN);
  adxl.powerOn();
  adxl.setRangeSetting(2);

  pinMode(BUZZER, OUTPUT);
  pinMode(RLED, OUTPUT);
  pinMode(YLED, OUTPUT);
  pinMode(GLED, OUTPUT);

  patternLength = loadPatternFromNVS(targetPattern);

  digitalWrite(YLED, HIGH);
  Serial.println("System Ready.");

  ESP32PWM::allocateTimer(0);
  lockServo.setPeriodHertz(50);
  lockServo.attach(SERVO_PIN, 500, 2500);
  lockServo.write(0);
}

// -------------------------------------------------------
void loop() {
  int x, y, z;
  adxl.readAccel(&x, &y, &z);

  float aMag = sqrt(
      sq(x * 0.0039) +
      sq(y * 0.0039) +
      sq(z * 0.0039)
  );

  float aDynamic = abs(aMag - 1.0);
  unsigned long now = millis();

  if (aDynamic > KNOCK_THRESHOLD) {
    if (now - lastKnockTime > 100) {
      knockTimes[knockCount++] = now;
      lastKnockTime = now;
      Serial.printf("Knock #%d detected.\n", knockCount);
    }
  }

  // Timeout detect → check pattern
  if ((now - lastKnockTime > PATTERN_TIMEOUT) && knockCount > 1) {
    checkPattern();
    resetPattern();
  }

  delay(10);
}

// -------------------------------------------------------
void checkPattern() {
  if (patternLength <= 0) {
    Serial.println("⚠ No valid pattern loaded.");
    return;
  }

  if (knockCount < 2) return;

  // Convert times → intervals
  int intervals[MAX_KNOCKS];
  for (int i = 1; i < knockCount; i++) {
    intervals[i - 1] = knockTimes[i] - knockTimes[i - 1];
    Serial.printf("Interval %d: %d ms\n", i - 1, intervals[i - 1]);
  }

  int intervalCount = knockCount - 1;

  bool match = false;

  // ---------------------------------------------------
  // Sliding window with tolerance, allowing junk knocks
  // ---------------------------------------------------
  int minStart = max(0, -EXTRA_BEFORE);
  int maxStart = intervalCount - patternLength + EXTRA_AFTER;

  for (int offset = 0; offset <= maxStart; offset++) {

    int matched = 0;
    for (int j = 0; j < patternLength; j++) {
      int idx = offset + j;

      // out of recorded bounds? invalid
      if (idx < 0 || idx >= intervalCount) {
        matched = -1;
        break;
      }

      int diff = abs(intervals[idx] - (int)targetPattern[j]);
      if (diff <= KNOCK_TOL) {
        matched++;
      } else {
        matched = -1;
        break;
      }
    }

    if (matched == patternLength) {
      match = true;
      break;
    }
  }

  if (match) {
    Serial.println("✅ Correct knock pattern detected!");
    goodBeep();
    unlockBox();
  } else {
    Serial.println("❌ Pattern incorrect.");
    badBeep();
  }
}

// -------------------------------------------------------
void unlockBox() {
  Serial.println("🔓 Unlocking...");
  lockServo.write(180);
  delay(4000);
  Serial.println("🔒 Locking...");
  lockServo.write(0);
}

// -------------------------------------------------------
void resetPattern() {
  digitalWrite(YLED, HIGH);
  digitalWrite(GLED, LOW);
  digitalWrite(RLED, LOW);
  knockCount = 0;
  lastKnockTime = 0;
  Serial.println("Pattern reset.");
}

// -------------------------------------------------------
void goodBeep() {
  digitalWrite(YLED, LOW);
  digitalWrite(GLED, HIGH);
  tone(BUZZER, 1000, 150); delay(150);
  tone(BUZZER, 1500, 200); delay(200);
  noTone(BUZZER);
}

// -------------------------------------------------------
void badBeep() {
  digitalWrite(YLED, LOW);
  digitalWrite(RLED, HIGH);
  tone(BUZZER, 400, 200); delay(200);
  tone(BUZZER, 300, 250); delay(250);
  noTone(BUZZER);
}

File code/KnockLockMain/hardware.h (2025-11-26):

#ifndef HARDWARE_H
#define HARDWARE_H

#include <Arduino.h>       // Needed for Serial, digitalWrite, delay, HIGH/LOW
#include <Wire.h>
#include <Preferences.h>
#include <ESP32Servo.h>
#include <SparkFun_ADXL345.h>

extern Preferences prefs;

// Pins
extern const int SDA_PIN;
extern const int SCL_PIN;
extern const int SERVO_PIN;
extern const int BUZZER;
extern const int RLED;
extern const int YLED;
extern const int GLED;
extern const int BUTTON_PIN;

// Objects
extern ADXL345 adxl;
extern Preferences prefs;
extern Servo lockServo;

// Functions
void setupHardware();

#endif

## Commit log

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2025-10-22 IMU Testing + Prelim Partslist
    [Partslist_Group_PE04_1.xlsx]
2025-10-25 Schematic first draft, added datasheets, added partlist2 with some new components
    [ADXL345BCCZ-RL7.step, KnockLock.kicad_pcb, KnockLock.kicad_sch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]
2025-10-25 Organizing folders, added pcb (not done) and sch (first draft)
    [KnockLock.kicad_pcb, KnockLock.kicad_sch]
2025-10-25 version 1 for backup
    [KnockLockv1.0.kicad_sch]
2025-10-25 Reorganising KiCAD + Libraries
    [ADXL345BCCZ-RL7.step, CFR-25JT-52-10K.stp, CFR-25JT-52-4K7.stp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]
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2025-10-25 Minor Adjustments + Footprints
    [KnockLock.csv, KnockLock.kicad_sch]
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2025-10-26 v1.3 of schematic with servo motor connection
    [KnockLock.kicad_sch, Partslist_Group_PE04_2.xlsx]
2025-10-26 Fixed power gating
    [KnockLockV1.2.kicad_sch, KnockLockV1.3.kicad_sch]
2025-10-26 added NPN to BOM
    [Partslist_Group_PE04_2.xlsx]
2025-10-26 Updated diode for safety margin, added diodes and servo to Partslist_Group_PE04_2.xlsx
    [KnockLock.kicad_sch, KnockLockV1.3.kicad_sch, Partslist_Group_PE04_2.xlsx]
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2025-10-29 Reorganized schematic, added NPN for reset
    [KnockLockV1.4.kicad_sch]
2025-10-29 Shifting to USB port, so added port and UART, but UART not connected
    [KnockLock.kicad_sch, Partslist_Group_PE04_2.xlsx]
2025-10-30 Started Programming Interface
    - we need to be careful with the IO pin logic so we can use basic buttons to enter programming mode or if we should try to use transistors (maybe also use the other side of the D flip flop)
    [KnockLock.kicad_sch, KnockLockV1.4.kicad_sch]
2025-10-30 Reorganized, fixed pwr flags
    [KnockLock.kicad_sch]
2025-10-31 Schematic Prog
    - added buttons for programming interface
    - in V2 i removed flip flop for deep sleep mode operation
    [KnockLock.kicad_sch, KnockLockV1.5.kicad_sch, KnockLockV2.0.kicad_sch]
2025-10-31 Minor Update to V1.5
    - added RC delay for reset button
    [KnockLock.kicad_sch, KnockLockV1.5.kicad_sch]
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2025-11-02 Sch V2.1
    ### Programming Interface
    - Added pull up for the EN pin so it normmaly high
    - Switched the push button for the boot to pin headers for a jumper
    ### Power Safety
    - Added some decoupling capacitors to the end of the voltage regulator
    - added a fuse PFRA 110 (used 0ZRE0012FF footprint cause close enough)
    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
    [KnockLockV2.1.kicad_sch, Partslist_Group_PE04_2.xlsx]
2025-11-02 V2.1 adjustments
    - added all footprints
    - added all components to BOM
    [KnockLock.csv, KnockLock.kicad_sch, KnockLockV2.1.kicad_sch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]
2025-11-03 Some minor changes - removed 2nd set of decoupling capacitors after voltage regulator, formatting
    [Partslist_Group_PE04_2 - With HSRW.xlsx, Partslist_Group_PE04_2.xlsx]
2025-11-03 Added back decoupling capacitors
    [KnockLockV2.2.kicad_sch]
2025-11-03 Fixed footprint for Piezo
    [KnockLock.kicad_sch, KnockLockV2.2.kicad_sch]
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2025-11-05 Made first draft of pcb design, modified existing library symbol, changes to BOM, changes to schematic
    [KnockLock.kicad_pcb, KnockLock.kicad_sch, KnockLockV1.0.kicad_pcb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]
2025-11-05 Minor adjustments to PCB design, fixed DRCs
    [KnockLockV1.1.kicad_pcb]
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2025-11-06 First draft of routing complete, parts list updated, 3d models added, button changed
    [AutoBOMForChecking.xlsx, KnockLock.csv, KnockLock.kicad_pcb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]
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2025-11-07 Updates to PCB Dft
    - I added some labels on the silkscreen for the boot and UART pins
    - Cleaned up the voltage regulator circuit
    - Made sure everything connets to the ground plane
    - added some GND vias
    [KnockLock.kicad_pcb, KnockLock.kicad_sch]
2025-11-08 Plotted pdf, changed to female pin headers, minor tweaks
    [KnockLock.kicad_sch, KnockLockV1.3.kicad_pcb, KnockLockV1.4.kicad_pcb]
2025-11-08 PCB Net Fixes
    - made the ground planes more connected for better dissipation and flow
    - fixed an error where we had a 3V3 net and 3.3V net, switched to 3.3V net so everything is now properly connected
    [KnockLock.kicad_sch, KnockLockV1.5.kicad_pcb]
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2025-11-09 Minor Updates and Export of 3D Model Pics
    [KnockLock.kicad_pcb]
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2025-11-12 Major Updates
    - moving the ESP32 to the edge with a keep out zone
    - adding a button for a programming mode
    - changing resistors and 0.1uF capacitors to SMT
    - increasing signal track sizes from 0.3 to 0.5
    - re-routing to accomodate better decoupling
    [KnockLockV2.0.kicad_pcb, KnockLockV5.0.kicad_sch, aisler-2-layer-simple-drc.kicad_pcb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]
2025-11-12 Conflict Fix
    [KnockLock.kicad_pcb, KnockLock.kicad_sch]
2025-11-12 Ensuring Proper Clearance Setttings
    [KnockLock.kicad_pcb]
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2025-11-13 PCB Final Touches
    - added the logo
    - added mounting holes
    - double checked DRC against AISLER reqs
    [KnockLock.kicad_pcb, KnockLock.kicad_sch]
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2025-11-15 Thermal Adjustments
    - added some additional vias to the heat sink of the MCU for better thermal relief into the button ground plane
    [KnockLock.kicad_pcb]
2025-11-16 Updates to 3D Model
    - I made sure each component has a 3D model
    - I changed the JST connector to the one the Lab has
    [KnockLock.kicad_pcb, KnockLock.kicad_sch]
2025-11-17 First Draft of Housing
    - created a basic safe
    - created a door with mounting holes, space for LED diffusion and built in button
    - still need to do the hinge pins + slot for servo latch
    [HInge Pin_s2v2.stl, Hinge_s2v2.stl, KnockLock.kicad_pcb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]
2025-11-17 Fixed many DRC errors, updated power supply connection to a JST 2.50mm
    [KnockLockV2.1.kicad_pcb, KnockLockV5.1.kicad_sch]
2025-11-18 Added holes for LEDs and Piezo for louder sound
    [HInge Pin_s2v2.stl, Hinge_s2v2.stl, KnockLock_Box.SLDPRT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]
2025-11-18 fixing final ERC errors
    [KnockLockV5.2.kicad_sch]
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2026-01-07 Code fixed, no allowed mistakes anymore
    [batteryMonitoring.cpp, config.h, hmi.cpp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]
2026-01-08 fixes to 3D model
    [BatteryCover.SLDPRT, BatteryCover.STL, ButtonPress.SLDPRT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]
2026-01-09 Fixed mistake tolerance, added better comments, fixed button model
    [ButtonPress.SLDPRT, ButtonPress.STL]
2026-01-12 Small fix to values
    [config.h]
2026-01-14 Presentation done, first draft, 3d model, reading style changed
    [BatteryCover.SLDPRT, BatteryCover.STL, ButtonPress.SLDPRT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]
2026-01-14 Fixed config, images organized, ppt updated, excel sheet for feedbacks
    [UserFeedback.xlsx]
2026-01-15 Methdology Progress
    + images for schematics, theory and housing design
    + work distribution for writing
    * heading numbers and some figures
    [KnockLockV6.1.kicad_sch]
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2026-01-17 verification and validation defined
    + all test specifications defined
    + More information for the BOM
    + completed all info for power consumption and battery life estimation
    [KnockLock_3D-Printing-Estimate.csv, power-consumption.xlsx]
2026-01-17 Software description done, Discussion done, Conclusion Done, BOM updated
    [KnockLockBOM.csv, KnockLock_Box_Bottom.STL, KnockLock_Box_Top.STL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]
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2026-01-17 fixing housing images
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2026-01-18 aesthetic changes
    + more transistion sentences
    - spelling issues
    + annotations to some images
    * fixed cost miscalculation
    + acknowledgement
    + abstract
    [HMI.xlsx, KnockLockBOM.csv]
2026-01-18 + extra slides in reserve, * minor fixes
    [KnockLockBOM.xlsx]
2026-02-08 Model fixes for hinges
    [BatteryCover.SLDPRT, BatteryCover.STL, ButtonPress.SLDPRT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]
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
